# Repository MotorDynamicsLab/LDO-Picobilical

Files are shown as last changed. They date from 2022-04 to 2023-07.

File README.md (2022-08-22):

# LDO Picobilical  
The Picobilical by LDO is a PCB mod designed specifically for the Voron0 series printers. The Picobilical is based on [V0-Umbilical](https://github.com/VoronDesign/Voron-Hardware/tree/master/V0-Umbilical) by timmit99 and retains its original advantages while introducing new features: 
- Rear mounted toolhead PCB simplifies toolhead wiring and maintenance.
- On-board RP2040 microcontroller frees up ports in the main controller while greatly simplifying wiring.
- Integrated 24V to 5V buck converter with max 5A output eliminates the need for an external 5V buck converter for the Raspberry Pi.
- Two independent neopixel ports and a buzzer.
- Selectable supply voltage (24V or 5V) for part fan and hotend fan.
- On-board thermistor for chamber temperature monitoring.
- On-board ADXL accelerometer for klipper input shaper.
- Optional filament sensor input.

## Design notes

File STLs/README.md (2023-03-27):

## Frame Cover Plate
This is a mandatory cover plate that sandwiches between the Picobilical frame PCB and the AB drive.

## Toolhead Spacer
This is a spacer that helps mount the toolhead PCB to the back of the extruder motor.
- Use the original toolhead spacer for users using the Mini Afterburner on the Voron0.1.
- Use the V0.2 toolhead spacer if you are building a Voron0.2 with a mini Stealthburner.

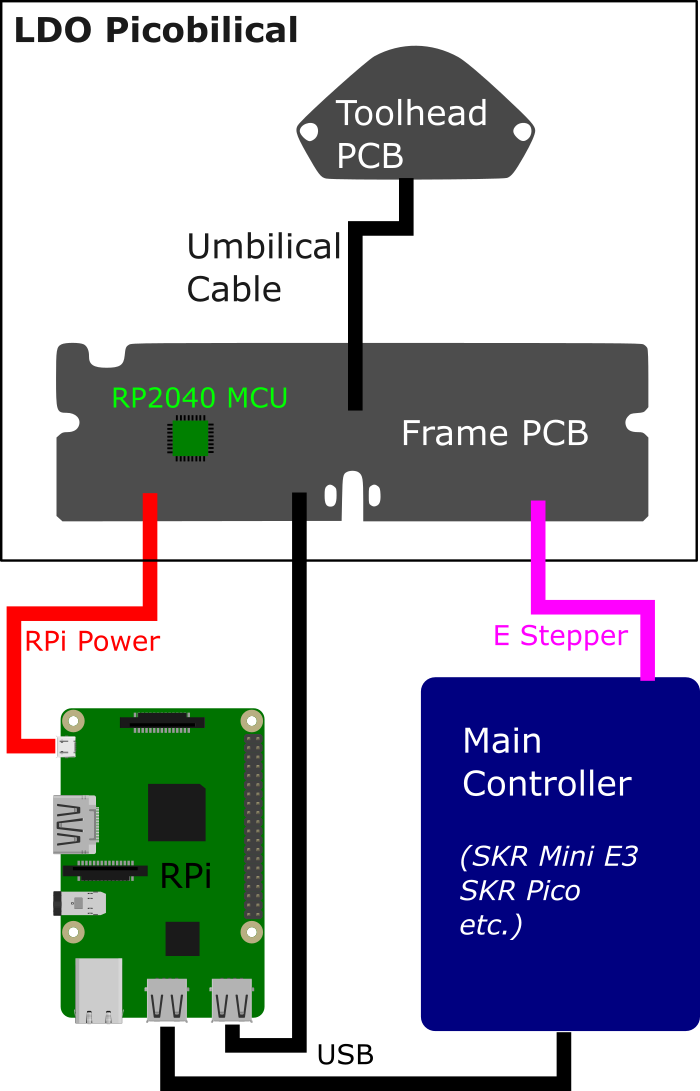
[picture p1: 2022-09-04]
Images/picobilical-block-diagram.png

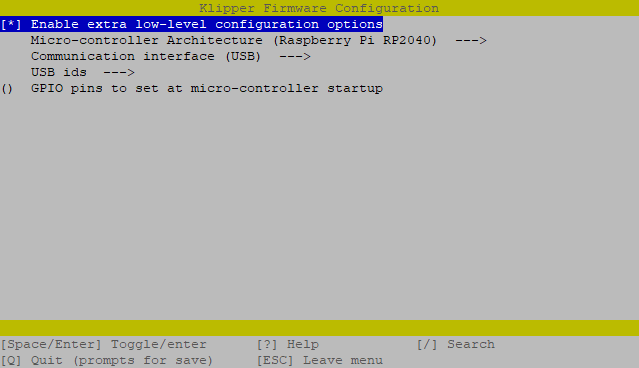
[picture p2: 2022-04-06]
Images/klipper_firmware_config.png

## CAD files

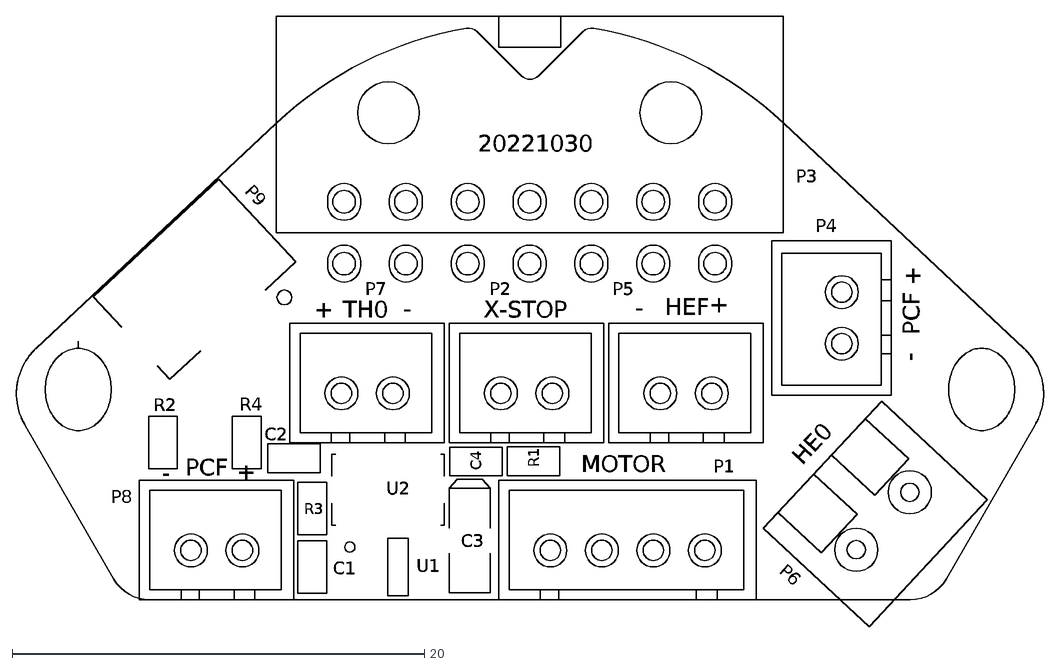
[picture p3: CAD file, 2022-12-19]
DXF/toolhead_pcb_outline.dxf
+
HEF
TH0
X-STOP
-
20221030
MOTOR
PCF
HE0
P4
P6
U2
U1
R4
R3
R2
R1
P9
C4
C3
C2
C1
P3
P8
P7
P5
P2
P1

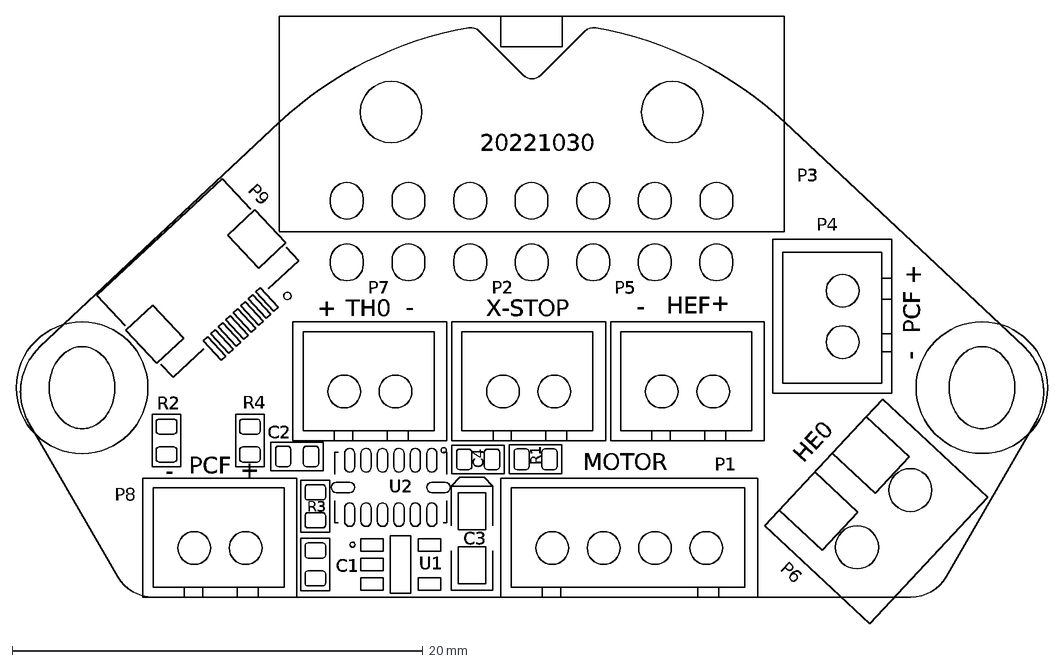
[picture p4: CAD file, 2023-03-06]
Hardware/Toolhead1.1/DXF/Picobilical Toolhead PCB Rev1.1.DXF
+
HEF
TH0
X-STOP
-
20221030
MOTOR
PCF
HE0
P4
P6
U2
U1
R4
R3
R2
R1
P9
C4
C3
C2
C1
P3
P8
P7
P5
P2
P1

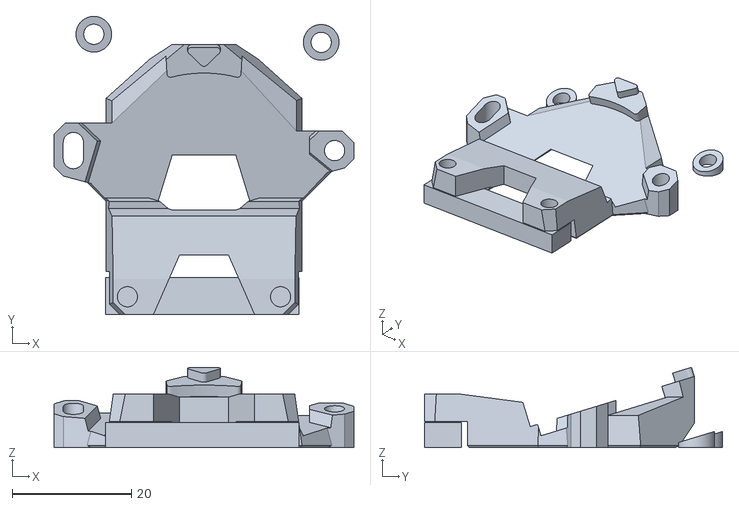
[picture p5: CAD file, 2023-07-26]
STLs/toolhead_spacer_v02.stl
50.3 x 50.0 x 13.5

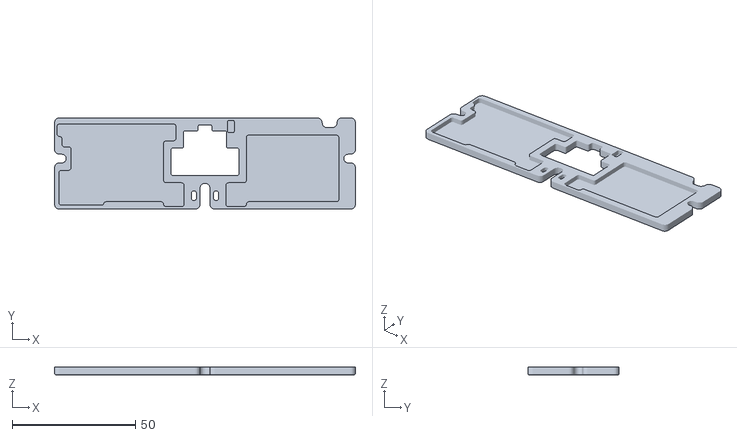
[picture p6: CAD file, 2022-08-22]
STLs/frame_cover_plate.stl
122.0 x 37.0 x 3.20

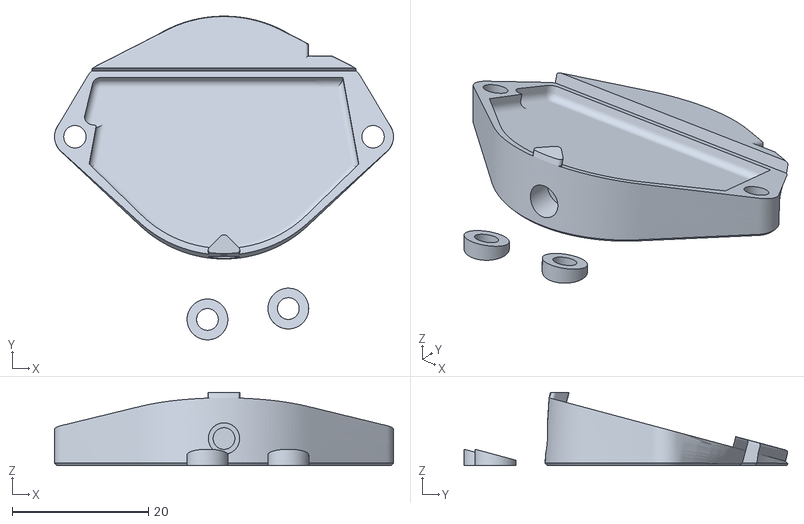
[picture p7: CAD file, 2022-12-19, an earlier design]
STLs/toolhead_spacer.stl
49.8 x 47.6 x 10.8

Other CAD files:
STLs/Frame Cover Plate.f3d
STLs/Toolhead Spacer V0.2.f3d
STLs/Toolhead Spacer.f3d

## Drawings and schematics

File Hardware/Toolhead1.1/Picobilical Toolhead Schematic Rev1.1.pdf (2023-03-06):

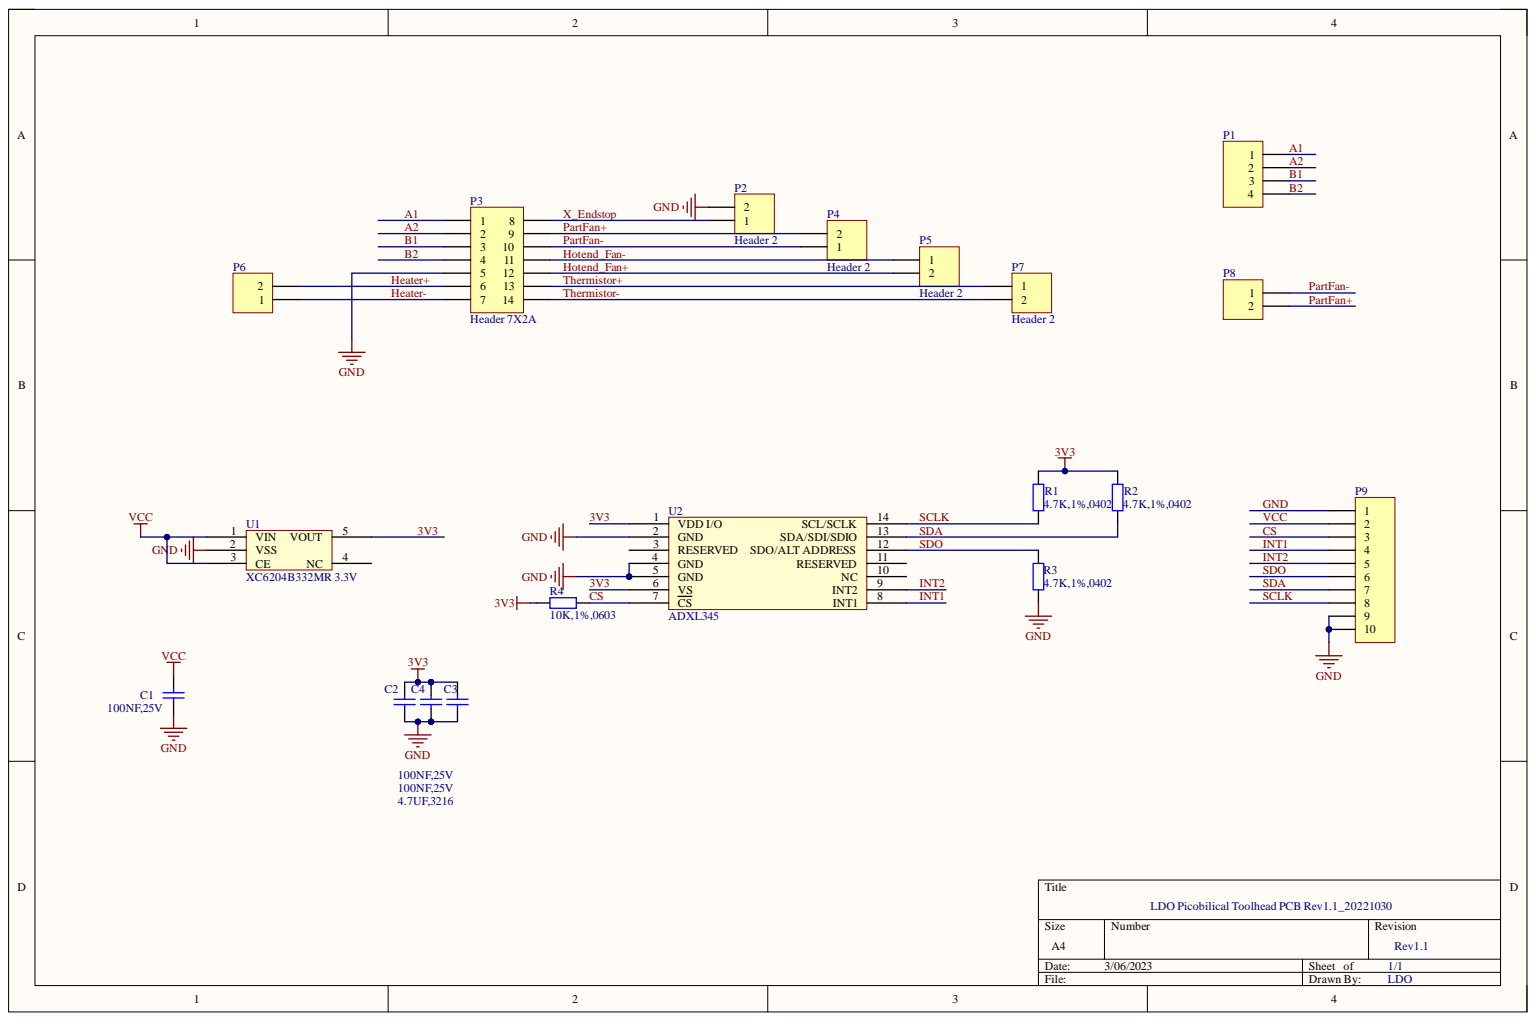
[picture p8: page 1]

LDO Picobilical Toolhead PCB Rev1.1_20221030

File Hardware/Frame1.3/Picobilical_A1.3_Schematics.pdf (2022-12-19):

1

2

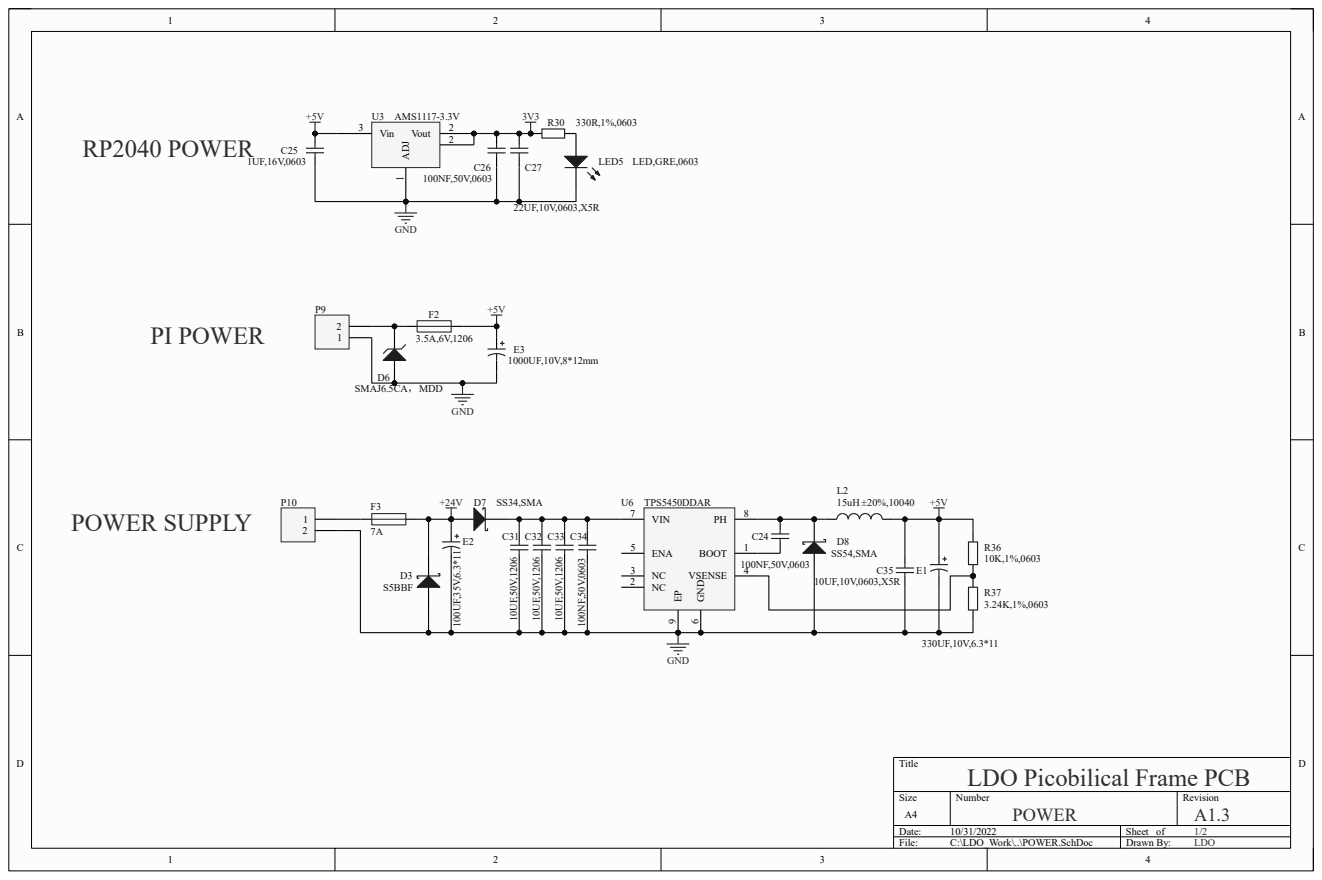
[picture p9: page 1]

Title
LDO Picobilical Frame PCB

Size A4 | Number POWER | Revision A1.3

Date: 10/31/2022 | Sheet of 1/2
File: C:\LDO_Work\..\POWER.SchDoc | Drawn By: LDO

## BootSel

# SPI Flash Heater

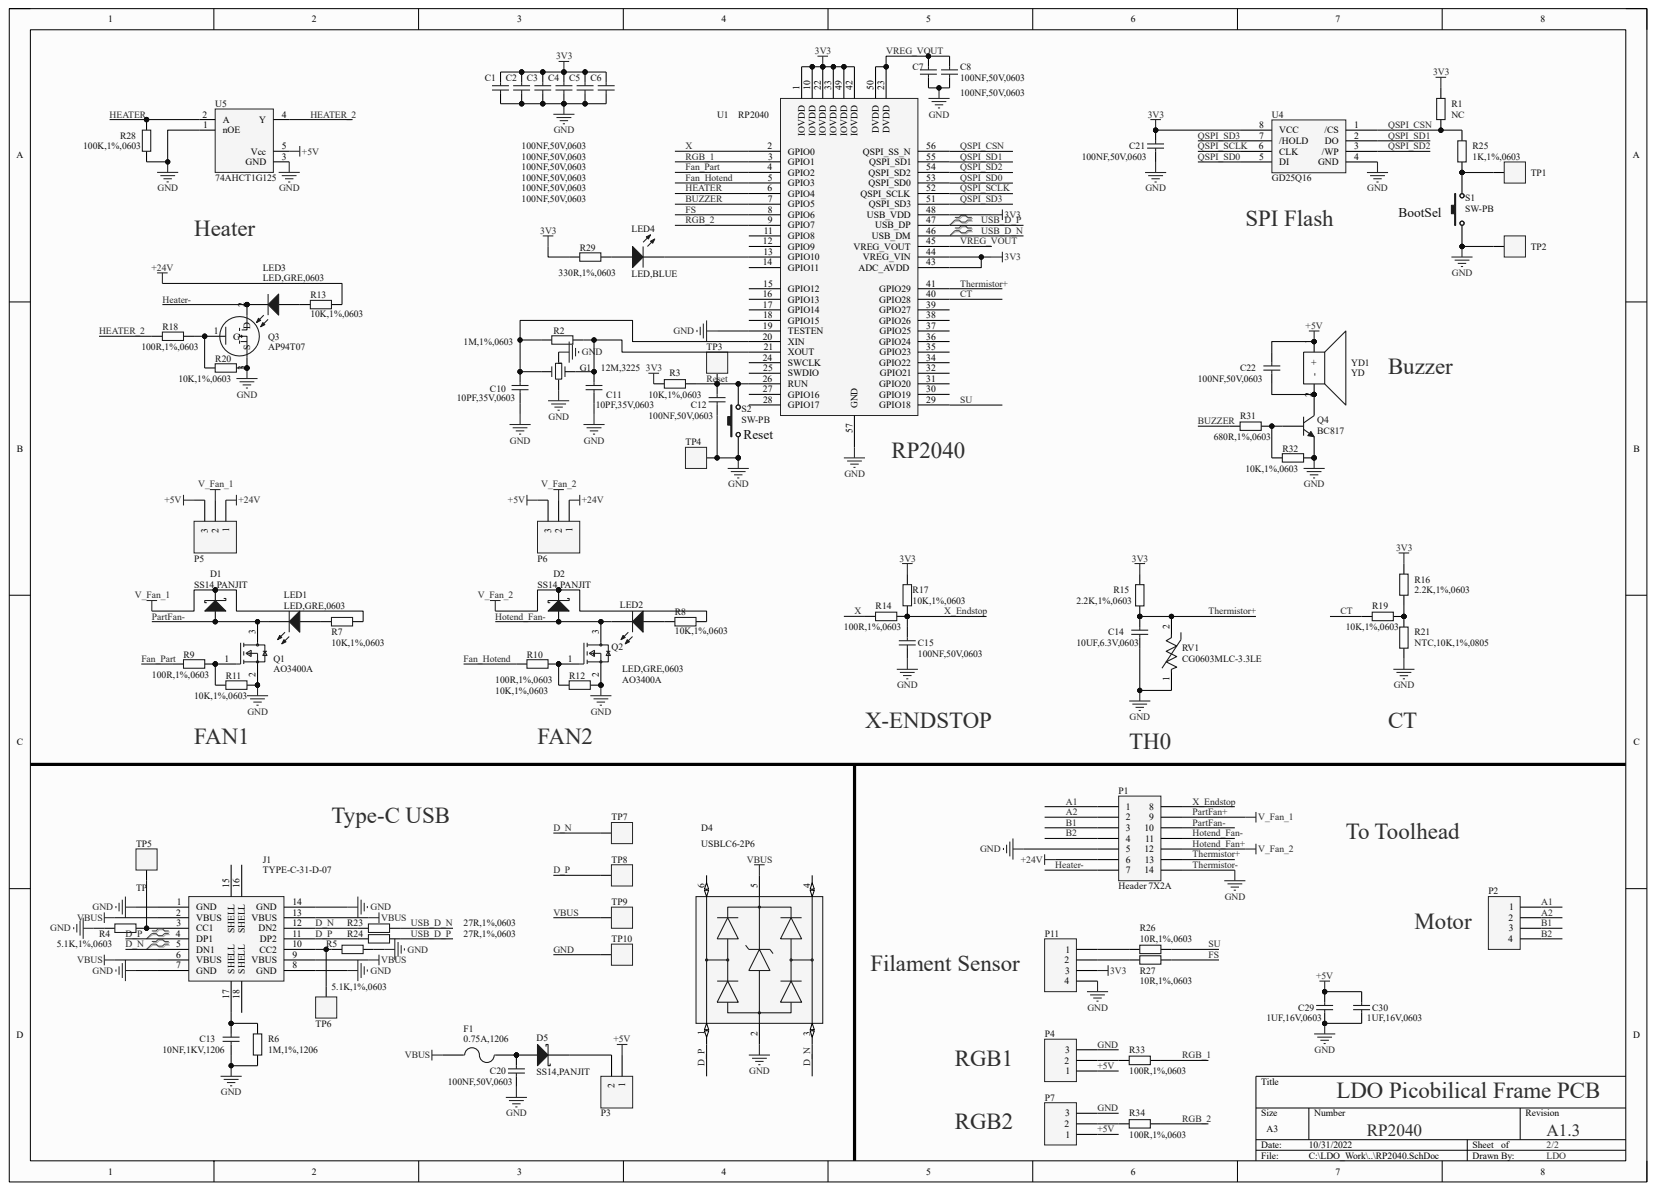
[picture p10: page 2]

GND
LDO Picobilical Frame PCB

Date: 10/31/2022 | Sheet of 2/2
File: C:\LDO_Work\..\RP2040.SchDoc | Drawn By: LDO

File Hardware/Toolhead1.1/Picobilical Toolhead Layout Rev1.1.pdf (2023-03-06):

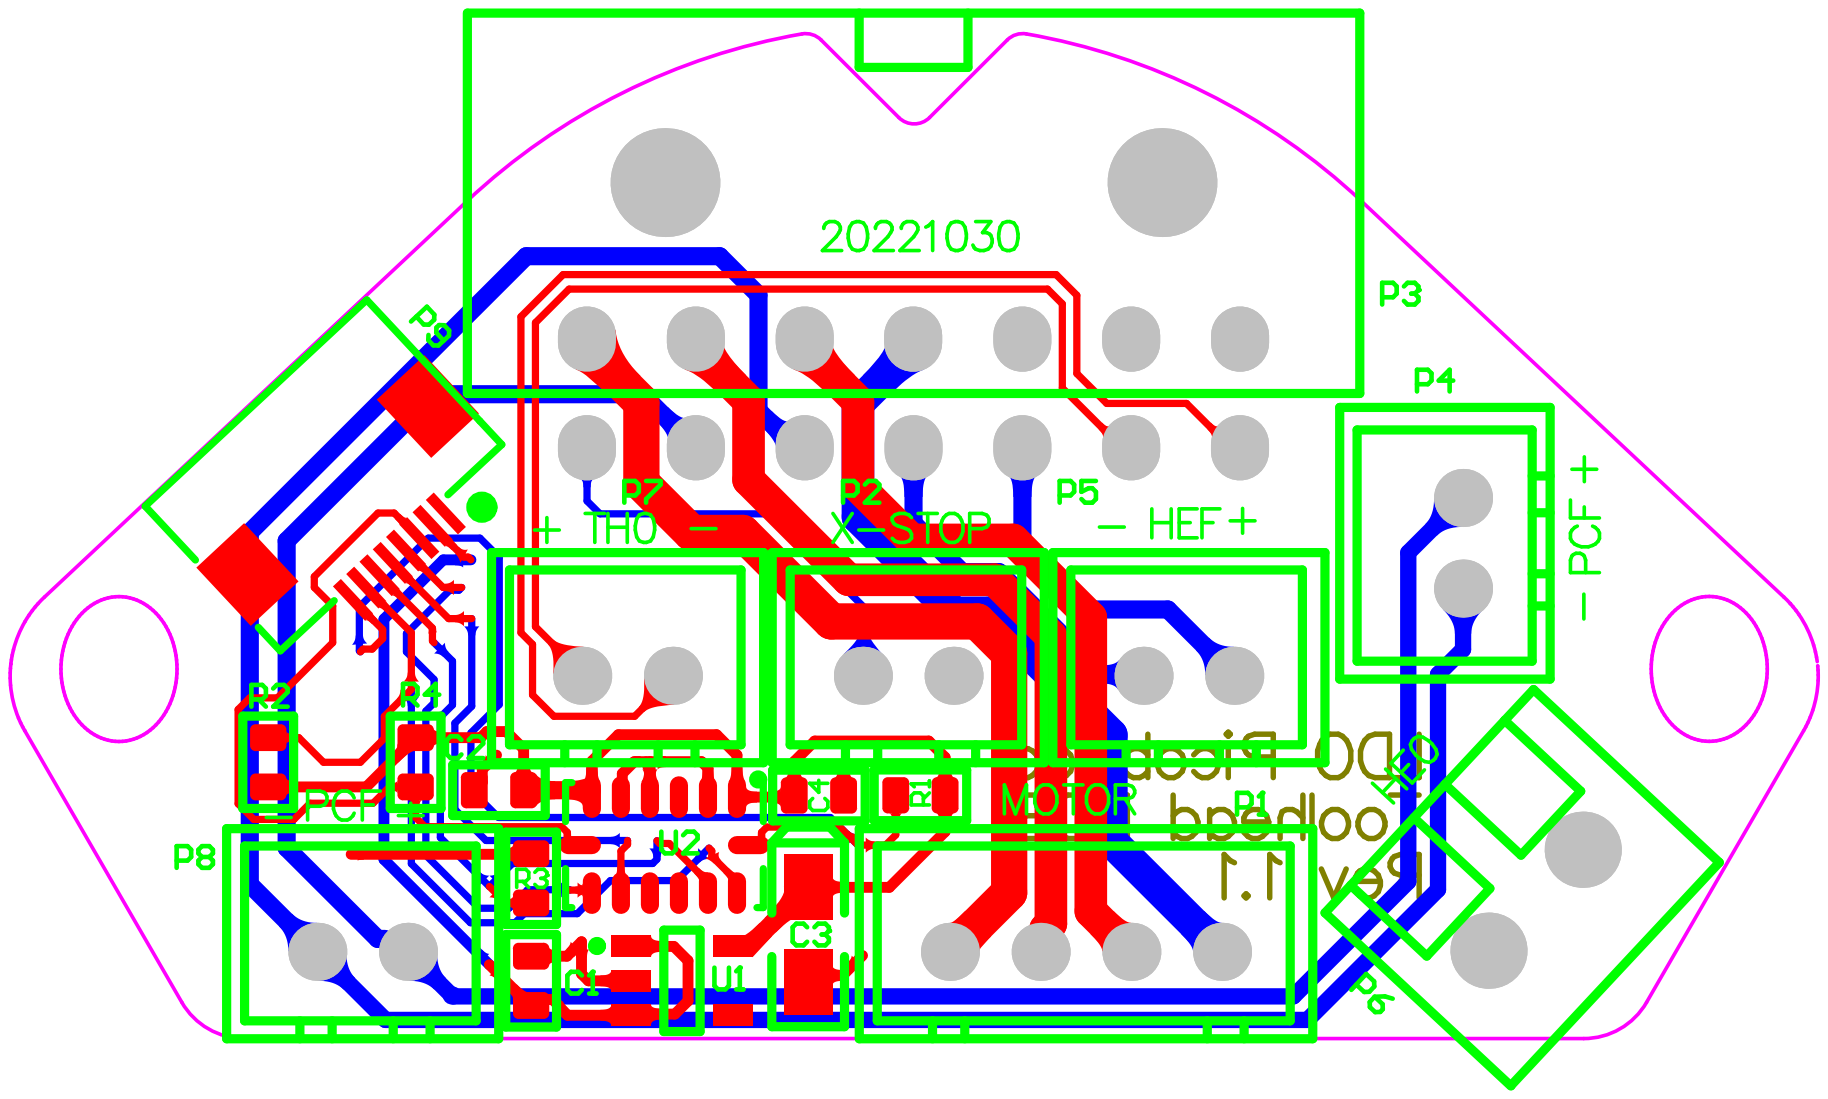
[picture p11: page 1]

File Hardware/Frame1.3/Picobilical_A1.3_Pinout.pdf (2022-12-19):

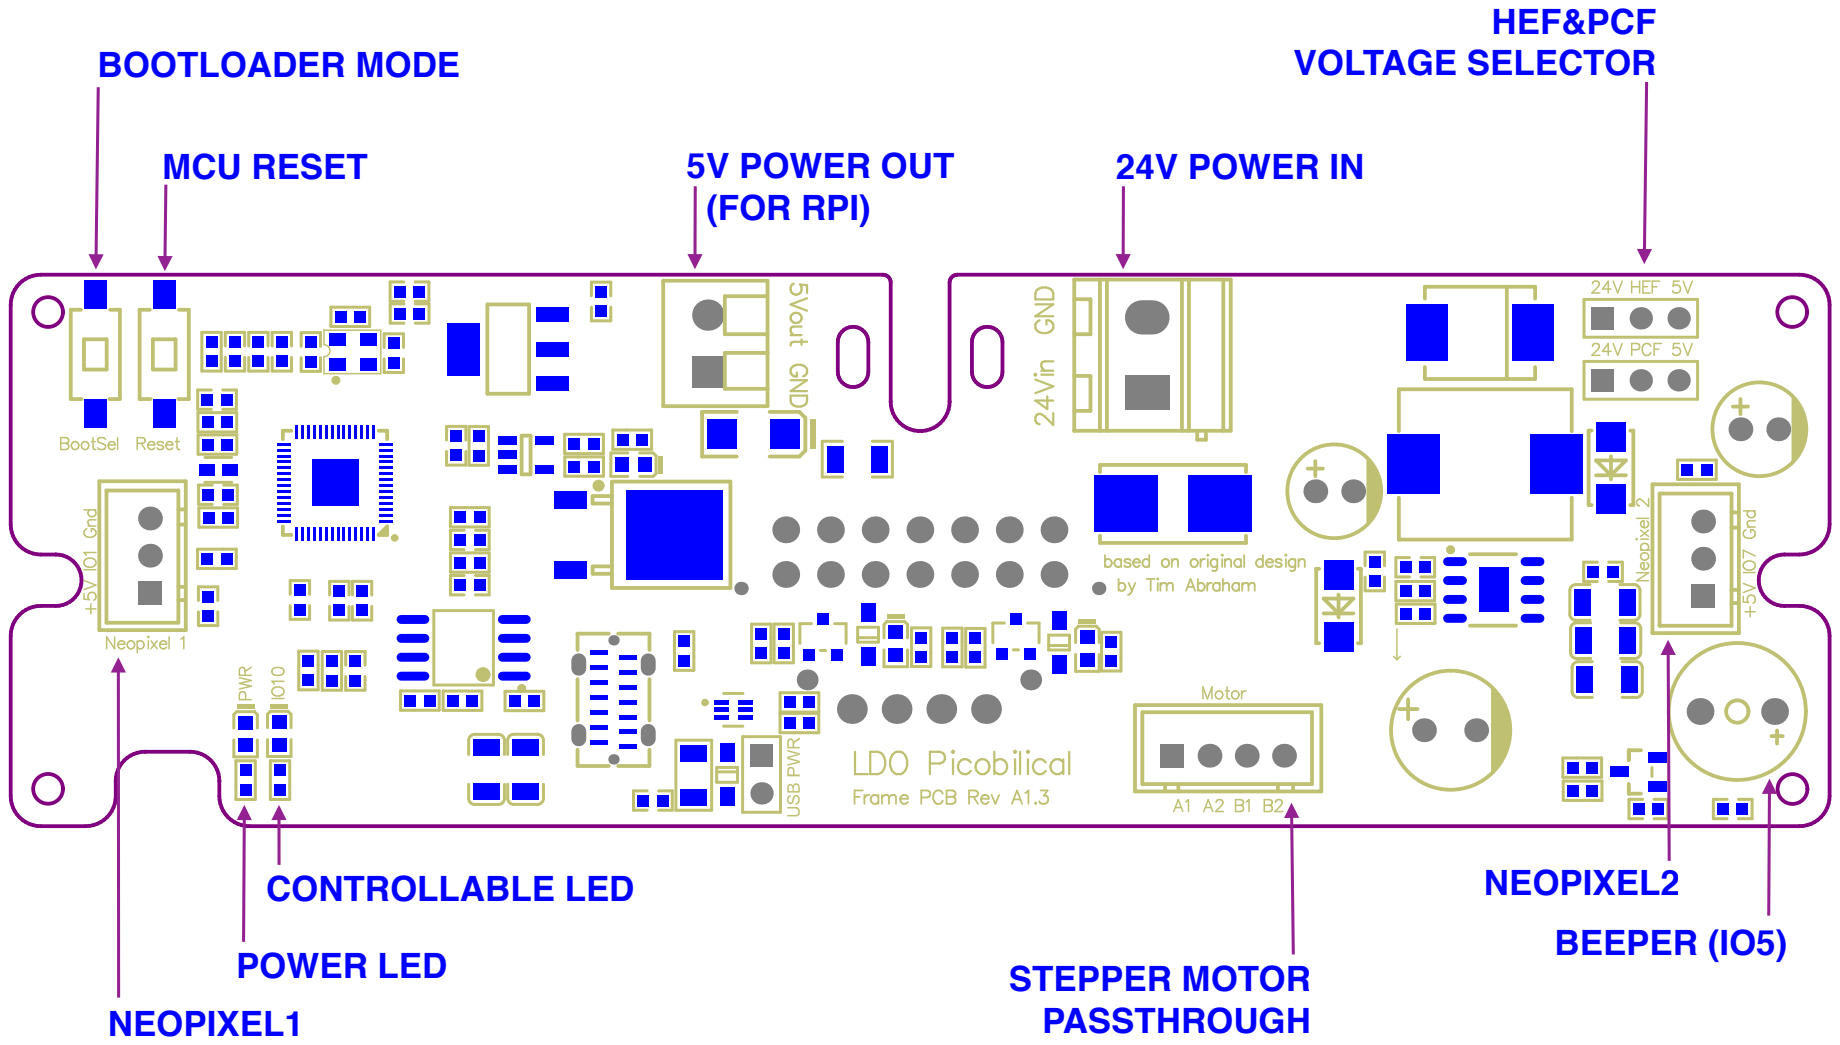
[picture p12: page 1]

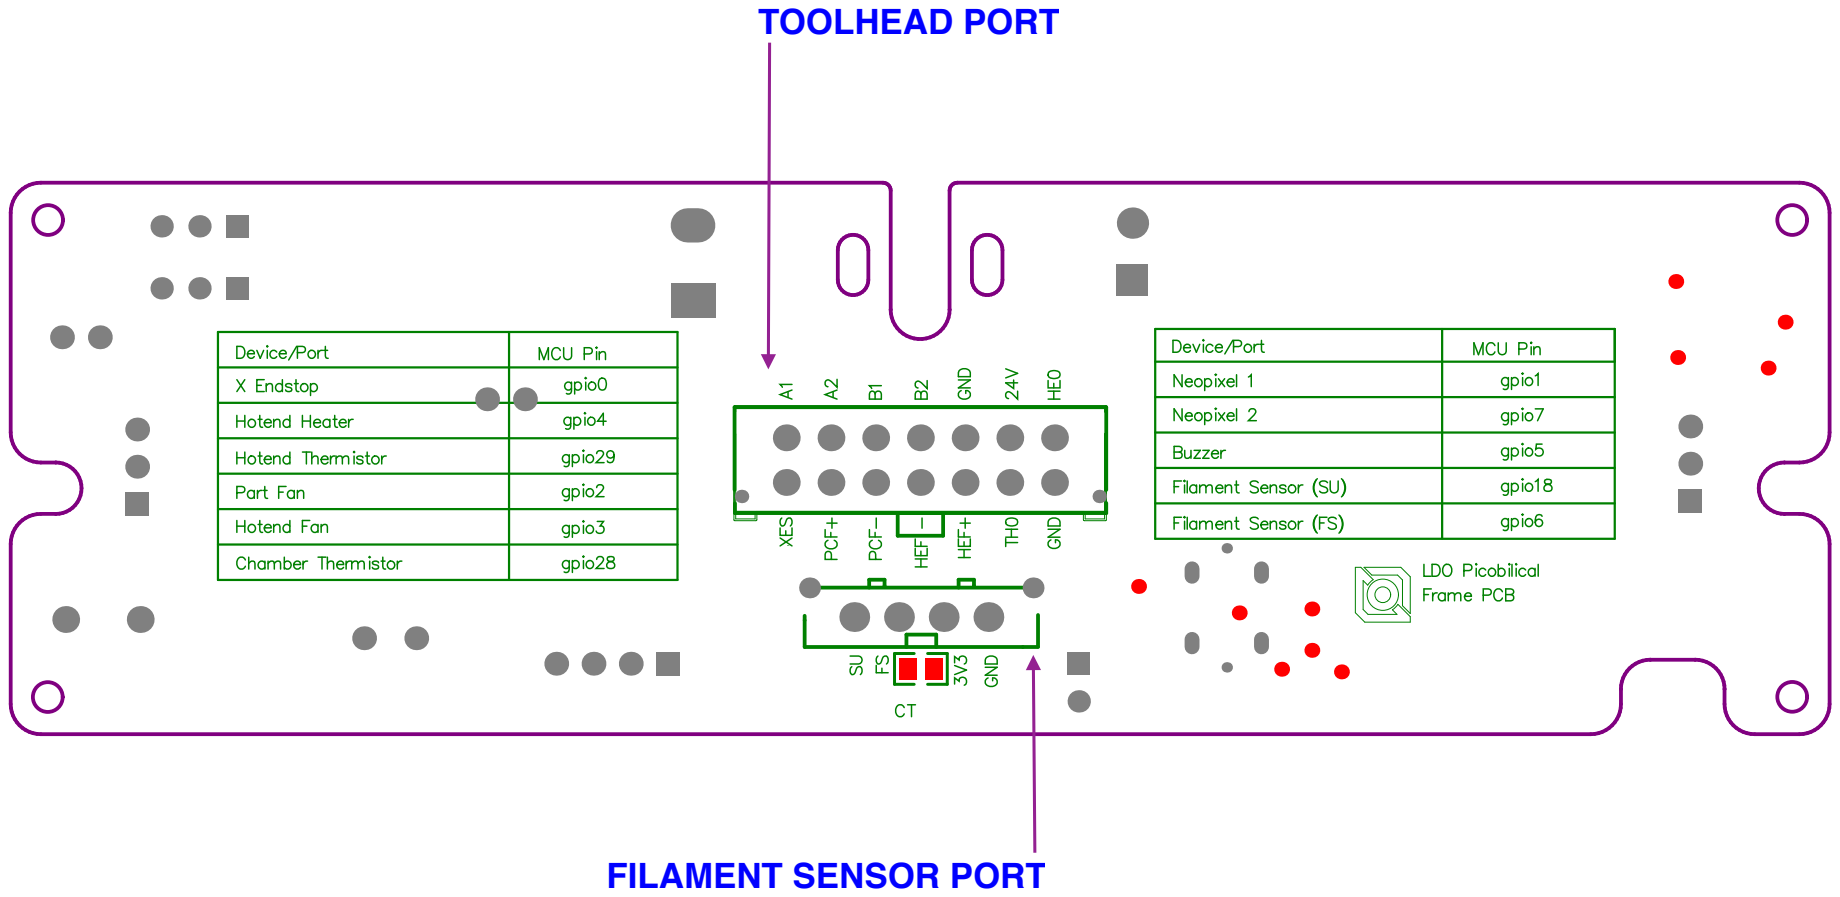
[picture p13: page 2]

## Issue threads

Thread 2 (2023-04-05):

V0.2 Toolhead Spacer

will-janz, 2023-04-05:
The [V0.2 toolhead spacer](https://github.com/MotorDynamicsLab/LDO-Picobilical/blob/master/STLs/Toolhead%20Spacer%20V0.2.f3d) has a few problems around it:

- The [Build Notes for V0-S1 + V0.2 Upgrade kit](https://docs.ldomotors.com/en/voron/voron01/build-faqv02) point to a different strain relief model (see note about page 180).
-  The [Printed Parts Guide (V0.2-S1 Kit Rev. A)](https://docs.ldomotors.com/voron/voron02/printed_part_guide_rev_a) links to the V0.1 version of the model.
- toolhead_spacer_v02.stl has the mount and a floating spacer in the same model.
- The new toolhead spacer/mount leaves a gap since the stock spacers don't fit, see attached image.
- It's unclear what the top hole is for.

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

chilipeppr, 2023-08-12:
I too am wondering what the top hole is for. I'm trying to wrap up my build and I keep thinking there needs to be more strain relief on the umbilical cord and that's what the top hole is for, but no part seems to match it. Anybody know?

chilipeppr, 2023-08-12:
Just following up, it seems to me the ideal part to screw into that M3 hole on the top of the LDO voron 0.2 picobilical toolhead_spacer_v02.stl is this top strain relief piece as its own part you can screw in.

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

nebulorum, 2023-10-20:
I saw this post and was wondering the same thing. Did you find a fix?

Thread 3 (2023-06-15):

Thermal runaway protection is not working

alexeypodrezov, 2023-06-15:
I've just discovered an issue with picobilical frame which is very concerning. I often leave my printer to print at night, and today I've discovered it at the morning with half-finished print with burned to black plastic at the point where nozzle were touching the model.
Turns out transistor, which controls hotend has burned down and picobilical were sending signal to heat it to maximum even if klipper was trying to turn it off
When electronic component is getting faulty, hotend should not be heating to the maximum - this is serious flaw which might create a disaster for someone else!

suedyx, 2023-06-16:
Hello Alexey,

It's Sue from LDO SUPPORT TEAM.
Sorry for this concerning issue happening.
Could you throw an email to sue.xiong@ldomotors.com with some pictures of the Frame PCB if you happened to take and your kit# that is engraved on a metal tag?
Issues like this always attract more attention from us and we hope our customers stay safe.
Thank you.

Best Regards,
Sue
LDO SUPPORT TEAM

suedyx, 2023-06-16:
Hello Alexey @alexeypodrezov  ,

It's Sue from LDO SUPPORT TEAM.
Sorry for this concerning issue happening.
Could you throw an email to [sue.xiong@ldomotors.com](mailto:sue.xiong@ldomotors.com) with some pictures of the Frame PCB if you happened to take and your kit# that is engraved on a metal tag?
Issues like this always attract more attention from us and we hope our customers stay safe.
Thank you.

Best Regards,
Sue
LDO SUPPORT TEAM

alexeypodrezov, 2023-06-19:
@suedyx , I sent an email with photos four days ago and haven't received any answer yet
Meanwhile, I replaced the faulty transistor, and the printer is working again, even though I'm afraid to leave it working without my constant attention, expecting a workaround here.

meistertek, 2023-12-31:
Has this issue been replicated at LDO with testing? I would think that a firmware update would address this issue, or does it require a hardware revision? Has this issue been addressed? For now would it be possible to skip the frame pcb and run the heater directly from the mainboard mosfet?

jamestattersall, 2024-06-10:
I have has the same thermal runaway. Extruder heater on max whenever system is powered up. Klipper detects heater temperature exceeding max and shuts down, but heater continues to run as long as system is powered up. Constant 24v on toolhead heater power pin.
Attached photo shows PCB and MOSFET with their IDs.
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

MaximilianFeld, 2025-07-29:
Had the same issue on my side now. Can you tell me how you identified the faulty transistor?

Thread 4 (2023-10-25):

Lost connection to mcu 'umb'

tonhe, 2023-10-25:
I started getting this error today on a new build. Google shows that there are a few people with the same issue, but I haven't seen anyone resolve it?

Zebebles, 2023-11-14:
I'd been getting this issue and tried a few things to fix it:
- Replace usb cables that connect the pi to both mcu
- Check the umbilical cable for broken wires at the molex connector crimps.  I had two wires that had broken.  I replaced the whole umbilical cable.

Im guessing it was the broken umbilical cable causing the issue, but replacing the usb cables can't hurt if you have spares laying around.

tonhe, 2023-11-14:
My issue ended up being the umbilical cable being lose on one end...

Closed 2023-11-14.

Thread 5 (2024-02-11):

Picobilical MCU does not appear in /dev/serial

mattmerritt215, 2024-02-11:
Hello,

I just finished setting up my new V0 kit but I’m having some trouble with Picobilical. I have everything wired up, but the controller doesn’t appear in /dev/serial/by-id also when I run “dmesg” it doesn’t appear to be recognized at all.

At first I thought it was maybe a USB problem, but I was able to flash the firmware to it over USB and my klipper host sees other USB devices just fine.

Can someone help?

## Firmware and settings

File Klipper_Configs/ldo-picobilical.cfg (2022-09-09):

# This file contains pin mappings for the LDO V0 Kit using the LDO Picobilical as a secondary controller.
# To use this config, the firmware should be compiled for the Raspberry Pi RP2040

# after running "make", copy the generated "klipper/out/klipper.uf2" firmware file 
# reboot the picobilical controller into BOOTSEL mode while connected to a PC, and copy the firmware file into the controller

## Voron Design VORON0 x LDO Picobilical partial config

## *** THINGS TO CHANGE/CHECK: ***
## MCU paths                            [mcu] section
## Thermistor types                     [extruder] sections

## *MAKE SURE* to include this partial config file *AFTER* the main controller config. 
## This will ensure the relavent sections are overwritten by the picobilical mappings specified here.

[mcu umb]
##  Obtain definition by "ls -l /dev/serial/by-id/" then unplug to verify
##--------------------------------------------------------------------
serial: /dev/serial/by-id/{REPLACE WITH YOUR SERIAL}
restart_method: command
##--------------------------------------------------------------------

#####################################################################
#   X Stepper Settings
#####################################################################

## XES - Toolhead PCB
## Overwrites the X endstop connection 
[stepper_x]
endstop_pin: umb:gpio0


#####################################################################
#   Extruder
#####################################################################

## HE0, TH0 - Toolhead PCB
## Overwrites the extruder heater & thermistor connection
[extruder]
heater_pin: umb:gpio4
sensor_type: ATC Semitec 104GT-2 # Change this to your actual thermistor type
sensor_pin: umb:gpio29
pullup_resistor: 2200


#####################################################################
#   Fan Control
#####################################################################

## PCF - Toolhead PCB
## Overwrites the part fan connection 
[fan]
pin: umb:gpio2

## HEF - Toolhead PCB
## Overwrites the hotend fan connection 
[heater_fan hotend_fan]
pin: umb:gpio3
heater: extruder
heater_temp: 50.0


#####################################################################
#   Neopixels
#####################################################################

## Neopixel 1 - Frame PCB
[neopixel rgb1]
pin: umb:gpio1
chain_count: 1
color_order: GRB
initial_RED: 0.3
initial_GREEN: 0.3
initial_BLUE: 0.3

## Neopixel 2 - Frame PCB
[neopixel rgb2]
pin: umb:gpio7
chain_count: 1
color_order: GRB
initial_RED: 0.3
initial_GREEN: 0.3
initial_BLUE: 0.3

## Buzzer - Frame PCB
[output_pin beeper]
pin: umb:gpio5
value: 0
shutdown_value: 0

[gcode_macro M300]
description: Custom M300 code to allow beeper to be used in gcode
gcode:
    {% set TIME_MS = params.P|default(100)|float %}
    SET_PIN PIN=beeper VALUE=1
    G4 P{TIME_MS}
    SET_PIN PIN=beeper VALUE=0

#####################################################################
#   Additional Sensors
#####################################################################

[thermistor CMFB103F3950FANT]
temperature1: 0.0
resistance1: 32116.0
temperature2: 40.0
resistance2: 5309.0
temperature3: 80.0
resistance3: 1228.0

## CT - Frame PCB
## Chamber thermistor
[temperature_sensor chamber_temp]
sensor_type: CMFB103F3950FANT
sensor_pin: umb:gpio28
pullup_resistor: 2200
min_temp: 0
max_temp: 100
gcode_id: chamber_th

## FS - Frame PCB
## Filament Sensor 1
#[filament_switch_sensor runout_sensor]
#switch_pin: umb:gpio6
#pause_on_runout: True

## SU - Frame PCB
## Filament Sensor 2
#[gcode_button filament_sensor_button]
#pin: umb:gpio18
# release_gcode: {INSERT YOUR GCODE HERE}

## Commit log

2022-04-06 add ldo-pico-umbilical.cfg partial config
    [ldo-pico-umbilical.cfg]
2022-04-09 add Frame Cover Plate
    [Frame Cover Plate.f3d]
2022-04-19 update cover plate to A1.1 version
    [Frame Cover Plate.f3d]
2022-04-27 add toolhead_pcb_outline.dxf
    [toolhead_pcb_outline.dxf]
2022-04-27 Add Toolhead Spacer
    [Toolhead Spacer.f3d, toolhead_spacer.stl]
2022-08-22 update Frame Cover Plate with clearances for buzzer
    [Frame Cover Plate.f3d, frame_cover_plate.stl]
2022-08-22 update Toolhead Spacer to tilted version
    [Toolhead Spacer.f3d, toolhead_spacer.stl]
2022-09-09 update ldo-picobilical.cfg with buzzer config, remove neopixel 3
    [ldo-picobilical.cfg]
2022-12-19 add pinout and schematics of A1.3 frame PCB
2022-12-19 update toolhead_pcb_outline.dxf to 20221030 version
    [toolhead_pcb_outline.dxf]
2022-12-19 update Toolhead Spacer with clearance for X endstop
    [Toolhead Spacer.f3d, toolhead_spacer.stl]
2023-03-06 move schematics and pinout to dedicate A1.3 directory
2023-03-06 add schematic layout & drawings for toolhead PCB
    [Picobilical Toolhead PCB Rev1.1.DXF]
2023-03-27 add new toolhead spacer for Voron 0.2
    [Toolhead Spacer V0.2.f3d, toolhead_spacer_v02.stl]
2023-05-08 fix floating washer in toolhead_spacer_v02.stl
    [toolhead_spacer_v02.stl]
2023-07-26 update spacer to account for occasionally protruding screw from rear of pancake motor
    [Toolhead Spacer V0.2.f3d, toolhead_spacer_v02.stl]
2024-10-16 CAD for PCBs
